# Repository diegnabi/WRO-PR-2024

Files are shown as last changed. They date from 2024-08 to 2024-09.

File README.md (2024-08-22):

Engineering materials
====

This repository contains engineering materials of a self-driven vehicle model participating in the WRO Future Engineers competition in the 2024 Open Regionals hosted in Puerto Rico.

## Content

* `t-photos` contains 2 photos of the team (an official one and one funny photo with all team members)
* `v-photos` contains 6 photos of the vehicle (from every side, from top and bottom)
* `video` contains the video.md file with the link to a video where driving demonstration exists
* `schemes` contains one or several schematic diagrams in form of JPEG, PNG or PDF of the electromechanical components illustrating all the elements (electronic components and motors) used in the vehicle and how they connect to each other.
* `src` contains code of control software for all components which were programmed to participate in the competition
* `models` is for the files for models used by 3D printers, laser cutting machines and CNC machines to produce the vehicle elements. If there is nothing to add to this location, the directory can be removed.
* `other` is for other files which can be used to understand how to prepare the vehicle for the competition. It may include documentation how to connect to a SBC/SBM and upload files there, datasets, hardware specifications, communication protocols descriptions etc. If there is nothing to add to this location, the directory can be removed.

## Introduction

Hello, we are part of Puerto Rico's team for the 2024 Open Regionals WRO Future Engineer category. The participants in this team are Diego Alejandro and Victor Gonzalez. Our robot was named Chappie from the movie Chappie.

Our ideas have changed over the last year since we went to Panama in 2023 to compete globally. We have also lost some of our team members to the difficult project. Luckily the team still stays together to keep competing and reaching new heights. 

Here we present our documentation for the upcoming Open Regional which includes every detail from 2024 onward.

* Part Choice

- Chasis

Chappie's chassis has gone through many different generations. Starting from 2023 when we competed with a Lego Spike we realised if we wanted to be taken seriously we had to completely renovate Chappie. Quickly we turned to using 3D printing since we could create any part and anyone with access to a 3D printer could recreate it. First, we set out to find some "case" for our components to mount them more easily to the yet-to-be-designed chassis. 

This proved useful but not time-efficient so when designing the first chassis we thought about putting together a breadboard to connect everything. We made holes in the first chassis which was a big box that at the top hosted the breadboard and the Arduino Mega. This didn't work out since adding the sensors and the wheels would be too bulky. Then we noticed that the breadboard could be held upside down and saved space. So the "zero gravity base" was created, it was a hole where a breadboard could be placed upside down and hold all of its components in place and the Arduino and battery could be placed at the top. This idea was taken to nationals and proved inefficient since the distance sensors would slip out of their contact and give us the wrong codes.

This is where our new design came into play, we kept it simple and used all the space available to accommodate all of the pieces.

- Hardware

Our first idea was to look for more open-source hardware that could yield more precise measurements. We decided on an Arduino Uno since we had the materials to work with it and our coach could teach us. Quickly we realised that an Uno did not have enough computing power so the idea of using the Arduino Mega or Raspberry Pi was asked. Since we had to get a 2024 national contender, we decided to stick with Arduino. The reason was that we already learned how to code in C++, and learning Python would take too long.

The HC-SR04 Ultrasonic sensors (distance sensors) were perfect since they gave precise measurements and had a ton of library support and guides on how to utilize them.

The MPU6050 accelerometer had a built-in gyroscope that we could use to keep the robot straight and turn exactly 90 degrees to the left or right. Again easy to work with for beginners with precise data output.

For our motor driver, we decided to use the L298N for the same reasons, at first we thought it was not necessary, but being able to go backward in tight spots proved to be useful, especially in the national competition.

Our driving motor is a TT DC Gearbox Motor which is very common and can be found anywhere. This also proved good with spending our resources since they were cheap.

The SG90 servo motor is a small and again easy-to-use servo with enough power to turn the wheels quickly and precisely. Again with good support.

We decided to eliminate the breadboard since its only real purpose was holding the distance sensors and gyroscope in place, and connecting everything through the power rails. We could connect everything through solder, which would hold everything together forever and not fall out. The other connection was straight from the Arduino to the corresponding sensor through a male-to-female jumper wire.

We used a switch to indicate whether the robot was going left or right and a push button to initiate the run attempt.

* Robot Base Improvements 

The new base of the robot (Chappie) is a simplified version of our national’s 2024 contender. We re-packaged everything into 2 floors, eliminated unnecessary components, and kept things simple for better performance and reliability. 

Chappie’s driving system’s only change was the axle but its steering system was completely re-designed to account for some major flaws such as being unable to steer away from the wall when it was too close. A TT DC Gearbox Motor powers the back wheels with a gear ratio of 1:48 which has an output shaft on each side. The driving motor will be controlled by the L298N motor driver. A small 9g servo motor has been placed at the front for the Ackerman steering system.

Our light sensor started to have some issues during the long times of the competition, sometimes it went higher than expected and activated the turn function, and other times it would be too low to trigger it at all. For this reason, we have decided to lower the robot as close as possible to the ground without scraping any parts. The sensor is placed in a hole which holds it in place. 

In our previous design, the battery placement was “terrible but needed” as it was a desperate measure to use the new battery. We have placed it at the bottom to lower its center of gravity. The base’s center has been widened to accommodate the size of the battery, also been elongated to fit the light sensor.

Chappie’s second floor consists of the L298N motor driver and Chappie’s brain, the Arduino Mega 2560 by Eleegoo.  The distance (ultrasonic) sensors will be connected looking left and right, glued onto the second floor. The gyroscope will be connected in a fixed position to get the most accurate readings possible. For our convenience, we have placed a buzzer to let us know when the robot is doing certain actions. 

* Problems we encountered with the new design

- Battery placement

The battery size has caused an increase of problems for us, we struggled a lot trying to find the most optimal space for it. Fortunately, through more testing of our design, we were finally able to put it in a spot we believe is the best possible.

We also thought to keep it as it was before on top of the robot, but we did that with our previous model and regretted it hugely since it would unbalance Chappie greatly and make him difficult to carry around. 

Our best option seems to be to increase the width of the first floor between the wheels since the battery is just about the same width. This idea would also prove useful since it gave the front wheels space to turn freely.\

The battery's weight was also too much for the small piece holding together the steering system, so we decided to move it back towards the driven wheels since they had a much stronger base.

- Steering System

The driving motor did not cause many problems but the steering motor did, especially because of our terrible steering system. Before we used to steer Chappie with 2 beams connecting each independent wheel, this would work and prove very efficient for tight turning with a wide amount of space available but whenever we had to turn quickly and away from the walls is where the problem arose. The steering system would hit the wall before it could get away from it, thus costing us many points. As well as having both motors under Chappie would make him very tall and our light sensor would be inconsistent.

Now the motors have been placed inside to reduce Chappie’s height, better handle it in the corners, get better consistent reading from the light sensors, and make it easier to carry around.

The steering system has now been changed to an Ackerman steering system so our wheels can remain in place and steer Chappie in tight places. This is in addition to changing our steering motor to a smaller servo, we found out that we do not need a strong beefy servo to steer Chappie. Now we have chosen the common 9g servo motor that can be commonly found.

The steering system's column that held it together was too thin and would fold under the Chappie's weight from its other components. Our solution was simple, first, we re-added the other column that was removed to make space for the servo and reinforced the column at the bottom so it would be less prone to bending, and added another column on top so that if it tried to bend the wheel hubs inward it wouldn't be able to.

The servo for the steering system has proved a bit annoying since its height and length are just barely out of reach from the steering joint thus forcing us to find different ways to place it (FIND SOLUTION HEIGHT). We fixed the length issue by turning the steering system so the joint would be looking inward rather than outward.

- Light sensor

The light sensor had to be at the bottom of Chappie and be as close to the ground as possible to get the most accurate readings. The problem we encountered was how were we going to get it through the base. 
Our first idea was to do what we did on the last model, make holes so only the contacts could peek through and hold it with the cables; it had worked before but it was very annoying so we kept testing. Then we thought about making a big hole to put the sensor through and hold it in place with the cables and some type of tape/glue. This would be a bit better but would be annoying to put together and probably not very good long term.
Our final idea and solution was to make a big enough hole to fit the hole sensor in and add pegs at the bottom to hold the sensor in place. This proved much easier to build and more efficient since the pins are more accessible and it stays in place without any other substance.

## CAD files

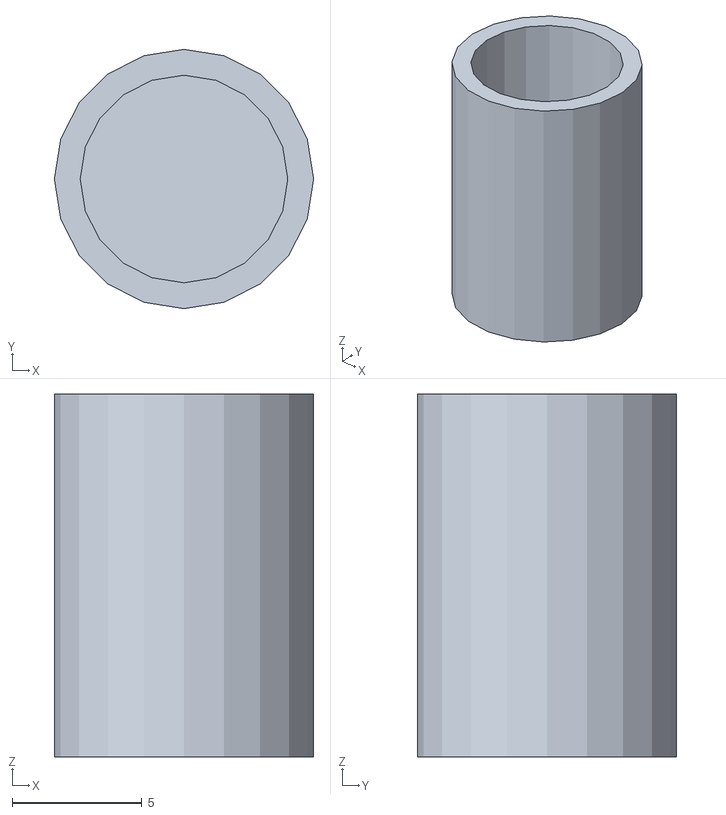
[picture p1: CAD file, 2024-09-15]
models/Capacitor Holder.stl
10.0 x 10.0 x 14.0

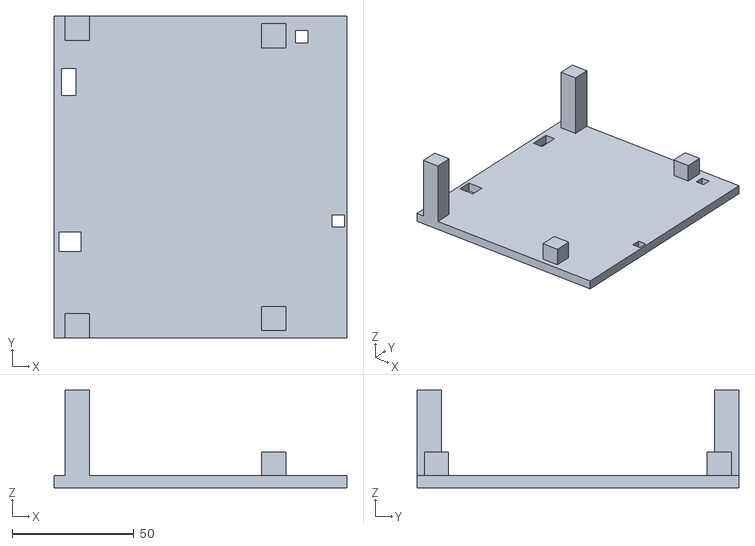
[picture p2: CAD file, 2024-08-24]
models/Top Plate With Cable Holes.stl
120.0 x 132.1 x 40.0

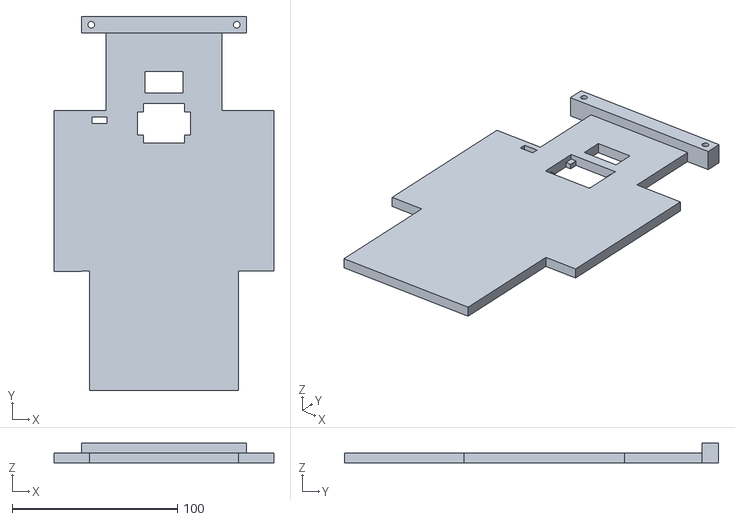
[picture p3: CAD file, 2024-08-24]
models/Base Plate Steering Column Attatched & Cable Holes.stl
133.0 x 226.5 x 12.0

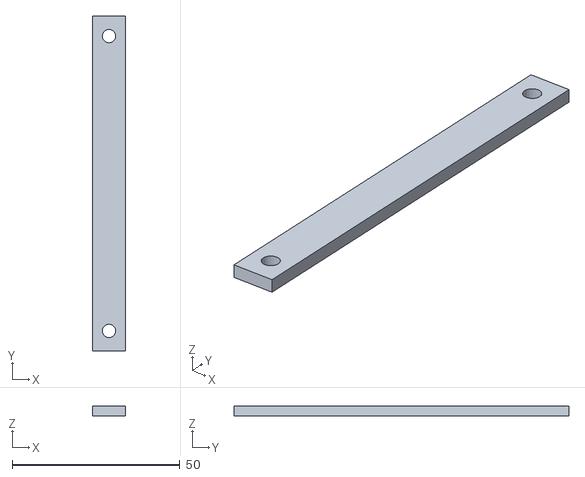
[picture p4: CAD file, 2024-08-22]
models/SteeringColumns (6).stl
10.0 x 100.0 x 3.00

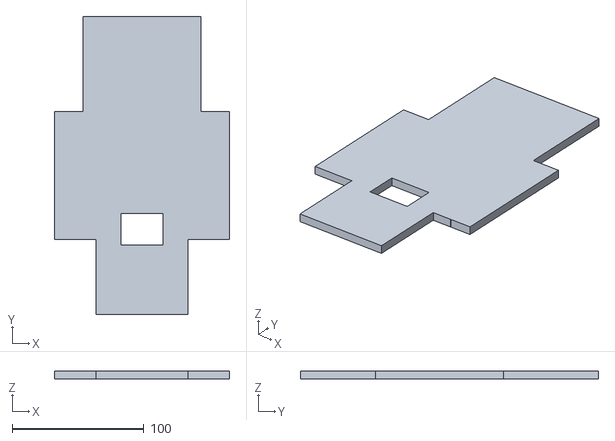
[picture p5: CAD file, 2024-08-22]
models/Base Plate.stl
133.0 x 226.5 x 6.00

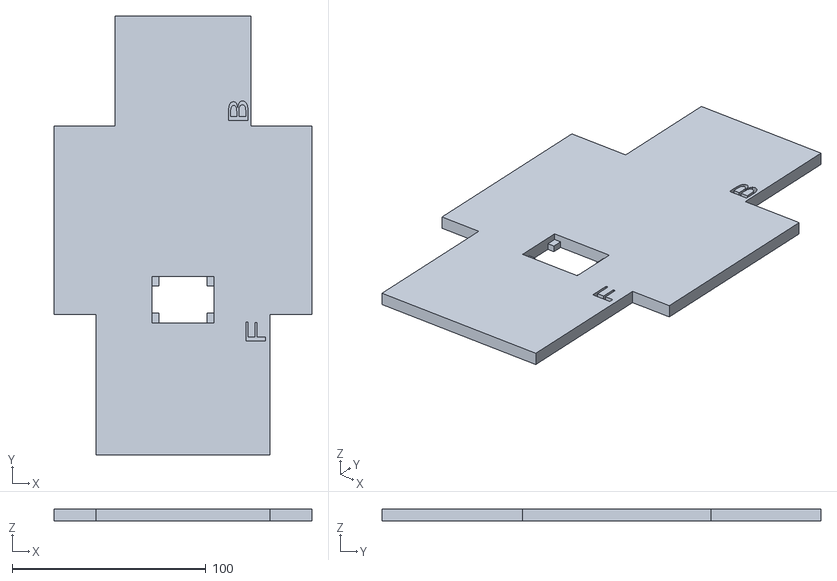
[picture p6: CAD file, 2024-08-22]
models/Base Plate Labeled (1).stl
133.0 x 226.5 x 6.00

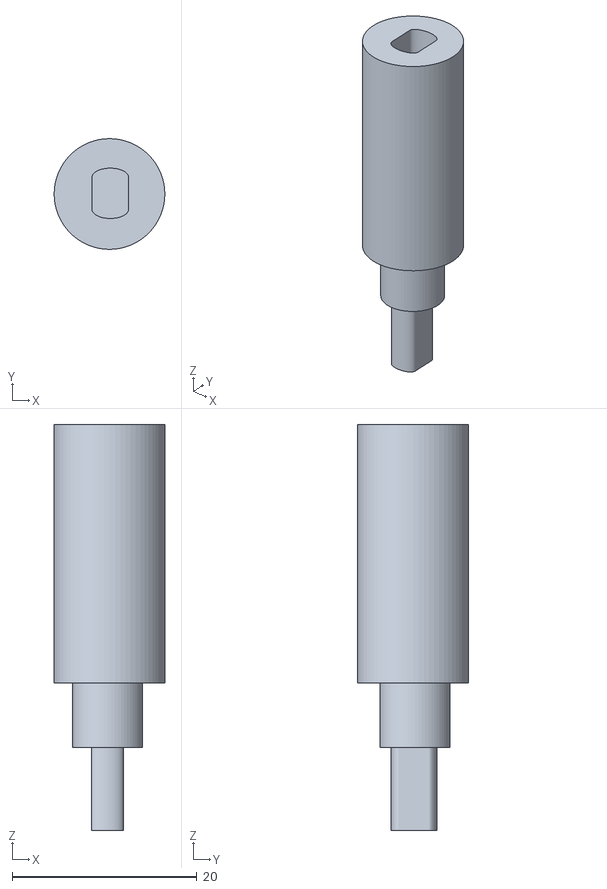
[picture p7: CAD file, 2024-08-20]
models/DrivingWheelShaft (11).stl
12.0 x 12.0 x 44.0

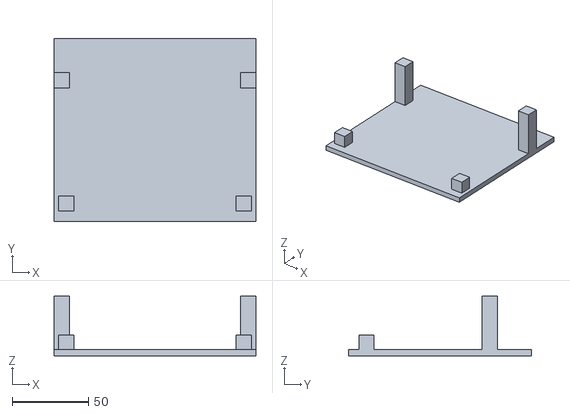
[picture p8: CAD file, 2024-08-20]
models/Top Plate.stl
132.1 x 120.0 x 39.0

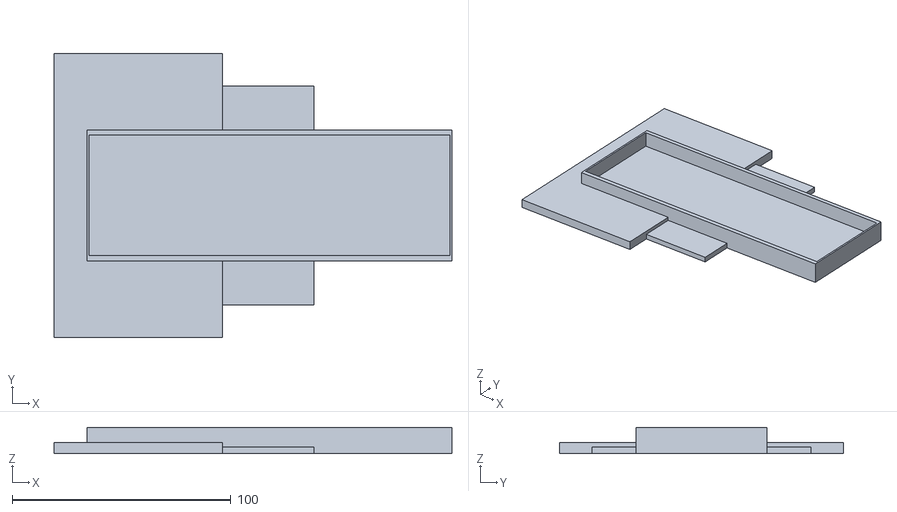
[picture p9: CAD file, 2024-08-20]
models/BreadboardCase&BatteryTray.stl
182.0 x 130.0 x 12.0

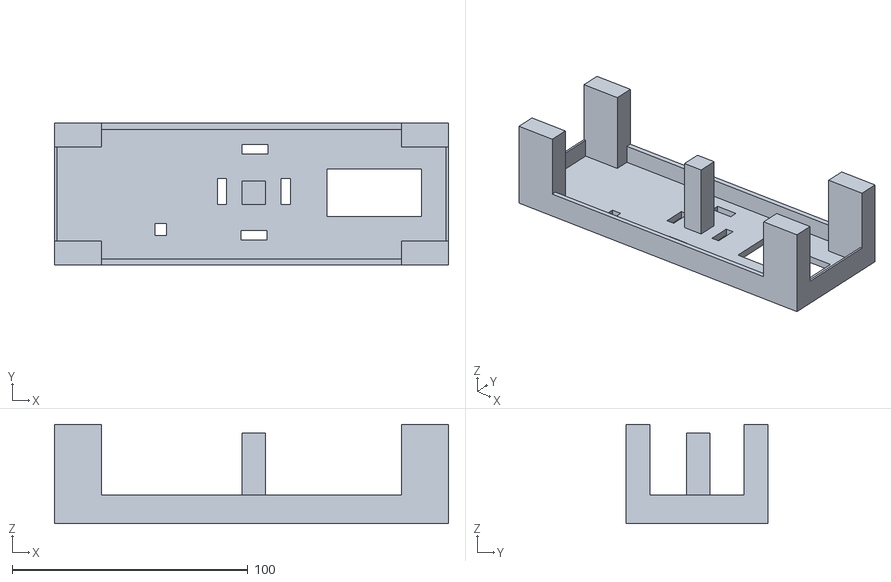
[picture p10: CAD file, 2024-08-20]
models/BottomBasePlatePV2 (5).stl
167.0 x 60.0 x 42.0

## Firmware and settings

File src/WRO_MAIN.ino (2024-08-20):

//Import Libraries
  #include <SR04.h>
  #include <NewServo.h>
  #include <SPI.h>
  #include <Wire.h>
  #include <MPU6050.h>
  #include <Adafruit_GFX.h>
  #include <Adafruit_SSD1306.h>


//Define Pin Number With Name Of Components
  //Defining Pin To Start Running The Program
    const int startButton = 13;

  //Defining everything needed for Left Distance Sensor
    const int L_TrigPin = 22; //Pin # for Trigger Pin
    const int L_EchoPin = 23; //Pin # for Echo Pin
    SR04 L_sr04 = SR04(L_EchoPin, L_TrigPin);
    long L_Dist; //Defining a Variable to Store the Data form the Left Sensor

  //Defining everything needed for Right Distance Sensor
    const int R_TrigPin = 53; //Pin # for Trigger Pin
    const int R_EchoPin = 52; //Pin # for Echo Pin
    SR04 R_sr04 = SR04(R_EchoPin, R_TrigPin);
    long R_Dist; //Defining a Variable to Store the Data form the Right Sensor

  //Defining Servomotor Pin #
    NewServo Steering(3);

  //Defining DC Motor Pin #
  const int in1 = 36;
  const int in2 = 37;
  const int ENB = 4;

  //Defining Pins for Color Sensor
    #define S0 30
    #define S1 29
    #define S2 26
    #define S3 27
    #define sensorOut 28

    #define S02 49
    #define S12 48
    #define S22 46
    #define S32 45
    #define sensorOut2 47

  //Defining Gyro name, variables and functions
    MPU6050 mpu;

    // Timers
      unsigned long timer = 0;
      float timeStep = 0.01;

    //Yaw values
      float yaw = 0;
  

//Define Variables Outside of Voids
  
  //Reset Corner Count to 0
  int corner = 0; 

  // Stores frequency read by the photodiodes of the color sensor 
  int red = 0;
  int green = 0;
  int blue = 0;
  int clear = 0;
  
  //Stores the "degree" value for the turning radius
  //int degree = 0;


void setup(){
  Serial.begin(115200); //Begin Serial Communication 

  //Setting up Servo Motor
  Steering.setMin(0); //Set Minimum Angle for Servo Motor
  Steering.setMax(180); //Set Maximum Angle for Servo Motor
  Steering.setInit(84); //Set Initial Position for Servo Motor
  Steering.begin(); //Start Servo Activity
  Steering.goInit(); //Servo Go To Initial Position

  // Setting the outputs
  pinMode(S0, OUTPUT);
  pinMode(S1, OUTPUT);
  pinMode(S2, OUTPUT);
  pinMode(S3, OUTPUT);
  pinMode(in1, OUTPUT);
  pinMode(in2, OUTPUT);
  pinMode(ENB, OUTPUT);
  
  // Setting the inputs
  pinMode(sensorOut, INPUT);
  pinMode(startButton, INPUT); //Indicate that "startButton" will be an input signal

  // Setting frequency scaling of the Color Sensor to 20%
  digitalWrite(S0,HIGH);
  digitalWrite(S1,LOW);

  // Initialize Gyroscope
  while(!mpu.begin(MPU6050_SCALE_2000DPS, MPU6050_RANGE_2G))
  {
    Serial.println("Could not find a valid MPU6050 sensor, check wiring!");
    delay(500);
  }

  // Calibrate gyroscope
  mpu.calibrateGyro();

  // Gyroscope Sensitivity
  mpu.setThreshold(1);

  //Drive Motor Foward
  digitalWrite(in1, HIGH);
  digitalWrite(in2, LOW);
  
}

void checkDist(){
  //Left Sensor Distance
  L_Dist = L_sr04.Distance();
  if (int (L_Dist)<11){ //If the Distance from the Left Sensor is Less Than 15cm
    Serial.println("Left side is close"); //Feedback in Serial Monitor
    digitalWrite(in1, LOW);
    digitalWrite(in2, HIGH);
    analogWrite(4, 150);
    delay(800);
    Steering.move(63); //Servo Go to Designated Angle
    digitalWrite(in1, HIGH);
    digitalWrite(in2, LOW);
    analogWrite(4, 150);
    delay(1000);
    Steering.goInit(); //Servo Go To Initial Position
    digitalWrite(in1, HIGH);
    digitalWrite(in2, LOW);
    analogWrite(4, 150);
    delay(500);
  } 

  else {
      Serial.println("Left side is far"); //Feedback in Serial Monitor
  }

  //Right Sensor Distance 
  R_Dist = R_sr04.Distance(); 
  if (int (R_Dist)<13){ //If the Distance from the Right Sensor is Less Than 15cm
    Serial.println("Right side is close"); //Feedback in Serial Monitor
    digitalWrite(in1, LOW);
    digitalWrite(in2, HIGH);
    analogWrite(4, 150);
    delay(800);
    Steering.move(95); //Servo Go to Designated Angle
    digitalWrite(in1, HIGH);
    digitalWrite(in2, LOW);
    analogWrite(4, 150);
    delay(1000);
    Steering.goInit(); //Servo Go To Initial Position
    digitalWrite(in1, HIGH);
    digitalWrite(in2, LOW);
    analogWrite(4, 150);
    delay(500);
  }

  else {
      Serial.println("Right side is far"); //Feedback in Serial Monitor
  }
}


void gyro(){ //Reads Gyro Yaw Angle Values
  timer = millis();

  // Read normalized values
  Vector norm = mpu.readNormalizeGyro();

  // Calculate Yaw
  yaw = yaw + norm.ZAxis * timeStep;

  //Output Yaw Angle
  Serial.print("Yaw = ");
  Serial.println(yaw);

  // Wait to full timeStep period
  delay((timeStep*1000) - (millis() - timer));
  
}

void Rturn() { //Turns the Robot 90 Degrees to the Right
  digitalWrite(in1, LOW);
  digitalWrite(in2, HIGH);
  delay(1000);
  Steering.move(62); // Turn right
  digitalWrite(in1, HIGH);
  digitalWrite(in2, LOW);
  delay(2060);
  checkDist();
  Steering.goInit();
  digitalWrite(in1, HIGH);
  digitalWrite(in2, LOW);
  delay(500);
  corner++; // Indicate a corner has been passed
}


void Lturn() { //Turns the Robot 90 Degrees to the Left
  digitalWrite(in1, LOW);
  digitalWrite(in2, HIGH);
  delay(1000);
  checkDist();
  Steering.move(107); // Turn right
  digitalWrite(in1, HIGH);
  digitalWrite(in2, LOW);
  checkDist();
  delay(2050);
  checkDist();
  Steering.goInit();
  digitalWrite(in1, HIGH);
  digitalWrite(in2, LOW);
  checkDist();
  delay(500);
  corner++; // Indicate a corner has been passed
}

void open() { //Code for Open Challenge
  int clear = 0;
  //    Min level of Light
  while (int (clear) <25){  //Whilst on the white part of track do the following)
    //CLEAR
    digitalWrite(S2,HIGH);
    digitalWrite(S3,LOW);
  
    // Reading the output frequency
    clear = pulseIn(sensorOut, LOW);
    delay(25);

    checkDist();

    //Drive Motor Foward
    digitalWrite(in1, HIGH);
    digitalWrite(in2, LOW);
    analogWrite(4, 150); //Speed of DC Motor
  }
  analogWrite(4, 180);
  Serial.println("OpenFinsih");
  Rturn();
}

void loop(){
  //If the Start Button has been Pressed then Run the Code until 12 Corners have been Completed
  if (digitalRead(startButton) == HIGH && corner < 12){
      //Run code here
      open();
  }
  if (corner >= 12) {
    digitalWrite(in1, LOW);
    digitalWrite(in2, LOW);
  }
}

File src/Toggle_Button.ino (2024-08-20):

//Define Pin Numbers to Components

const int button = 12;
const int led = 13;
int status = LOW;

void setup(){
pinMode(led, OUTPUT);
pinMode(button, INPUT_PULLUP); 
}

void loop(){

if (digitalRead(button) == HIGH) {
status = !status;
digitalWrite(led, status);
} 
while(digitalRead(button) == HIGH);
delay(50);
}

// == equal to
// = defining (what it means)

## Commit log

2024-08-20 National and Open Regional pieces
    Here are the pieces made in our 3D printer and used to compete in 2024
    [Back Plate.stl, BottomBasePlatePV2 (5).stl, BreadboardCase&BatteryTray.stl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]
2024-08-20 Code for the TCS230
    This code shows how the TCS 230 (our line sensor of choice) is utilized to give values of whether the robot has hit a line or is on a straight part of the track.
2024-08-20 Code for the distance sensors and servo movement
    This code contains the Serial feedback into the console and feedback through an OLED screen connected with I2c. This also moves the servo to steer away from any walls that might be close to it
2024-08-20 Test Servo connectivity
    Used to test that the servo was connected correctly and was functioning.
    [ServoTest.ino]
2024-08-20 Gyroscope correction and turning
    This code is used mainly to keep the robot running in a straight line, but can be modified to turn it 90 degrees
    [YawAngleServoCorrection.ino]
2024-08-20 Start/Stop button
    This code reads the HIGH/LOW signal from the pushdown button to determine when it starts its run or when it stops.
2024-08-22 Delete models/Front Plate.stl
    It will be printed in one complete piece so the separate ones are not needed.
    [Front Plate.stl]
2024-08-22 Delete models/Back Plate.stl
    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
    [Back Plate.stl]
2024-08-22 Base Plate for Chappie
    This is the main part of Chappie's chassis, here most of his components will be placed and the "Top plate" will rest on this piece as well
    [Base Plate Labeled (1).stl]
2024-08-22 Base Plate Battery Backwards
    This is the updated version where the battery is closer to the driven wheels and the light sensor is closer to the steering system.
    [Base Plate.stl]
2024-08-22 Steering Columns
    These hold the wheel hubs together. One at the top to hold it from bending in form the weight of the robot and the bottom one to connect it to the chassis.
    [SteeringColumns (6).stl]
2024-08-24 Base Plate - Attatched Steering Column
    This base plate has the steering column attached to the chassis for more sturdiness. Also, it has holes for the servo motor cables to go through.
    [Base Plate Steering Column Attatched & Cable Holes.stl]
2024-08-24 Top Plate - Cable Holes
    This top plate version has holes for all of the component's cables to go through the robot. Holes to hold the motor driver and gyroscope are also included in this version.
    [Top Plate With Cable Holes.stl]
2024-09-15 Capacitor holder
    This piece will hold the capacitor in place for the robot
    [Capacitor Holder.stl]
